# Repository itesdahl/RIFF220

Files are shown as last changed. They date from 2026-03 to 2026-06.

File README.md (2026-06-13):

# The RIFF220 DIY 3D printer
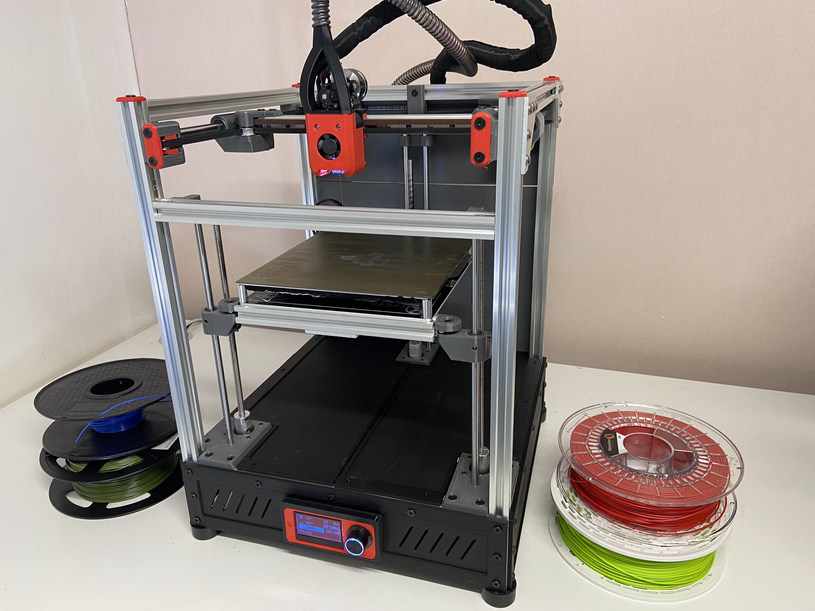
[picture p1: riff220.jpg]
Build


>[!NOTE]
>I recommend using second hand/recycled parts from old printers. It makes absolutely no sense to source all the parts new.

>[!TIP]
>Use the Voron Trident assembly guide to build the bed front arms and the A/B motor mounts. Please note that the orientation of some bolts are different from the original. You also have to replace one of the bolts with a 5mm shaft to allow the motor mout to sit flush to the top extrusion. https://github.com/VoronDesign/Voron-Trident/blob/main/Manual/Assembly_Manual_Trident.pdf Refer to the BFI idlers to print the original STLs for carrier and front. https://github.com/clee/VoronBFI
>

## Some key information the design and build:

- Max printable area 215x230x220, (X restricted by toolhead width)
- 2020 extrusions 
- 1x SKR Pico and 1x SKR 1.4 controller boards (not critical, use whatever you have that have enough drivers and can run Klipper)
- Radxa Rock 3C SBC (or a Pi. SBC with 3-4 USB ports recommended)
- MGN 12H rails/carriage X
- 10mm rods and bearings on Y 
- 8mm rods and bearings on Z 
- Corexy
- Klipper firmware 
- Triple z steppermotors (z-tilt functionality)
- Sensorless homing on X and Y 
- Dragonburner with Sherpa micro
- Low budget CPAP solution with 2 x 5015 fans (remix for ws7040 to get even more cooling)
- 1 x 240W 24V power supply

### Cutting extrusions

- 4x2020 500mm for Z 
- 8x2020 350mm for X and Y
- 1x2020 300mm for x-axis (supporting the MGN12 rail) 

### Extrusions for the bed assy in my build with a 220x220 base plate and a 214x214 24V heat bed
- 1x2020 268mm center (measure)
- 1x2020 220mm front 

>[!TIP]
>Check the frame for squareness and adjust/correct  as needed.
>Mount the 3 z-motor mounts with M5 10mm bolts. The motor mounts makes the frame more rigid. Check the frame again for squareness.

# Credits/sources for remixes
https://github.com/VoronDesign/Voron-Trident
https://github.com/clee/VoronBFI
https://github.com/chirpy2605/voron/tree/main/V0/Dragon_Burner

# Video part 1
https://youtu.be/kZbBAxifQg0

# Video part 2
https://youtu.be/Zv7GhpkNOPk

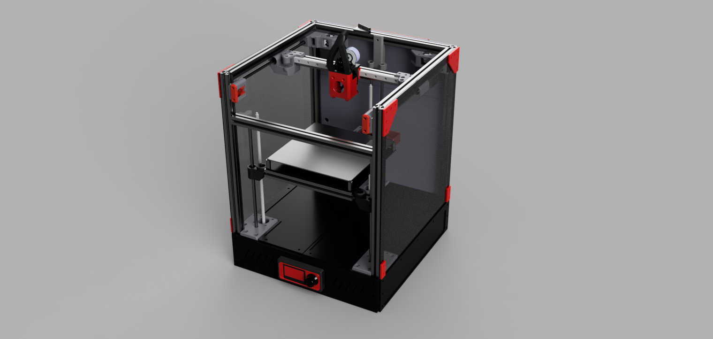
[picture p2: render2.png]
CAD model

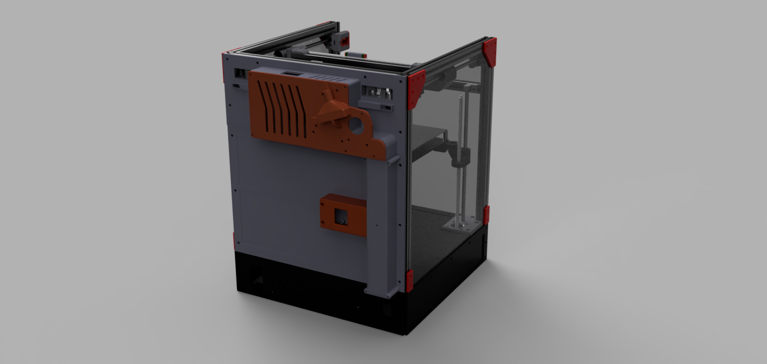
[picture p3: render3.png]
CAD model2


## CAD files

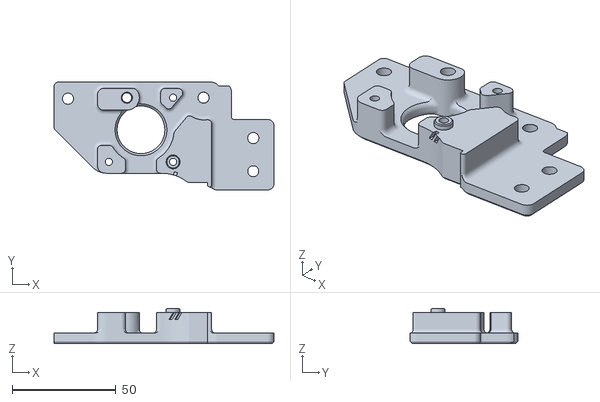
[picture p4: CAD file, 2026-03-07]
gantry/1x_rightmotor_lower.stl
106.2 x 52.0 x 17.0

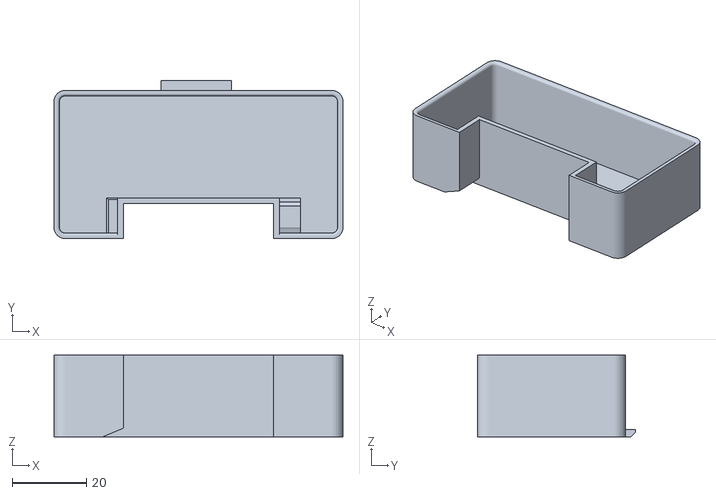
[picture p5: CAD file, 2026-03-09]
optional/1x_scrubber_bin.stl
78.0 x 42.7 x 22.0

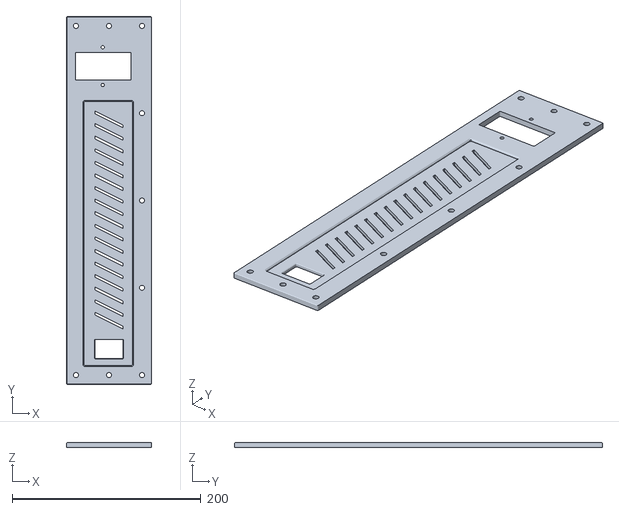
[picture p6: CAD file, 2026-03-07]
skirt/1x_rear_panel.stl
90.0 x 390.0 x 5.00

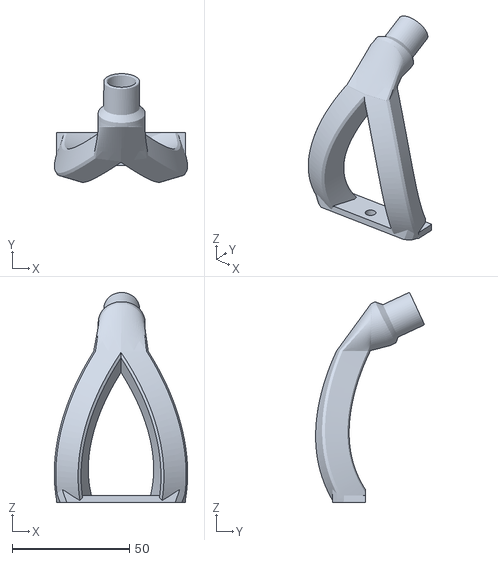
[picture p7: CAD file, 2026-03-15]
toolhead/cpap_adapter_v2.stl
56.9 x 46.4 x 89.5

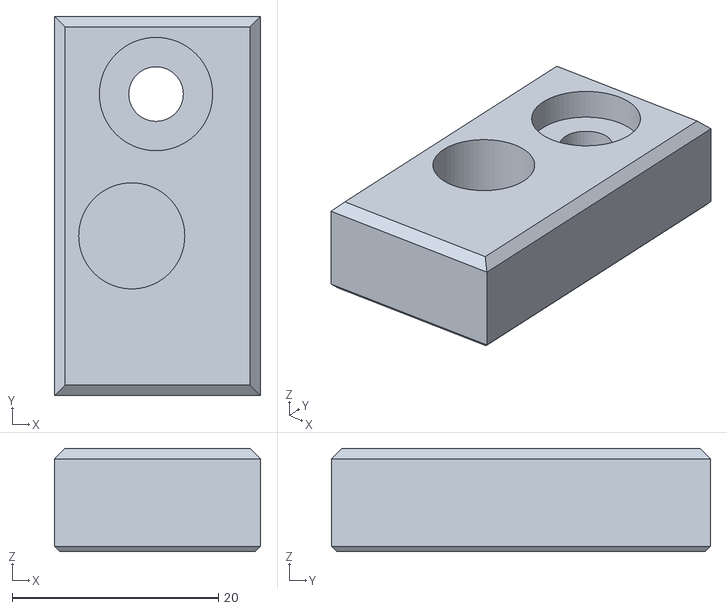
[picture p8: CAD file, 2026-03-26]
zaxis/1x_zrod_right.stl
20.0 x 36.8 x 10.0

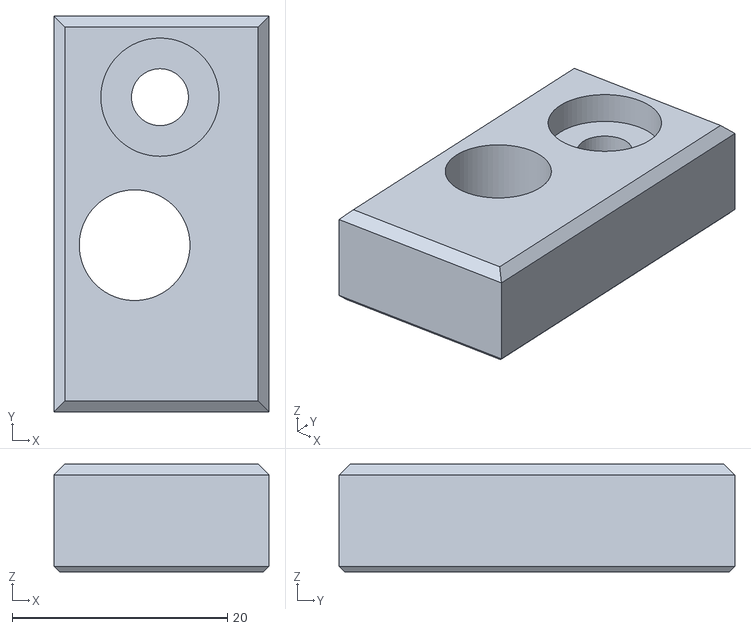
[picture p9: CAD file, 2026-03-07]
gantry/1x_yrod_right.stl
20.0 x 36.8 x 10.0

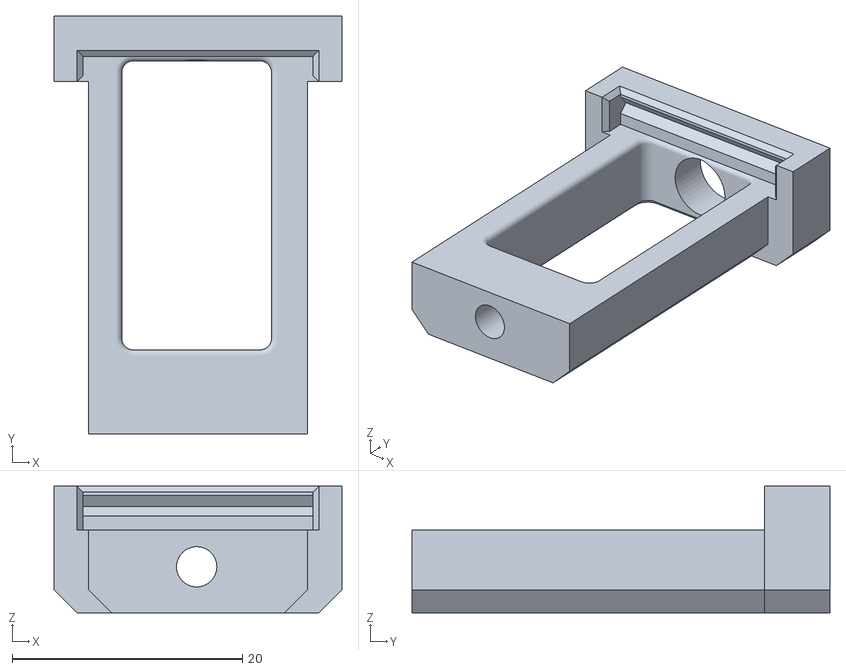
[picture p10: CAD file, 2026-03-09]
optional/1x_scrubber_holder.stl
25.0 x 36.3 x 11.0

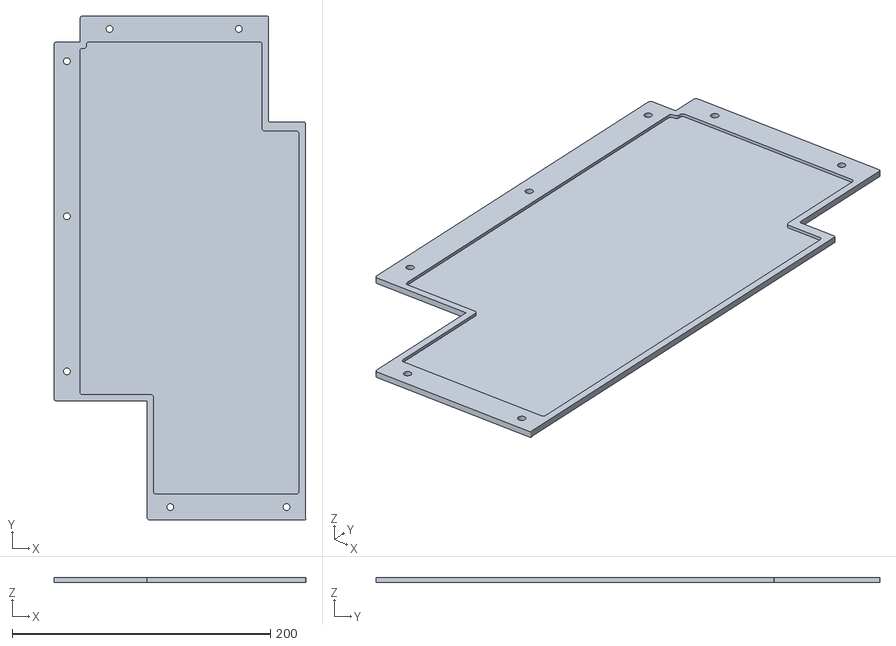
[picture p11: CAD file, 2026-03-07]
skirt/1x_left_top.stl
195.0 x 390.0 x 4.00

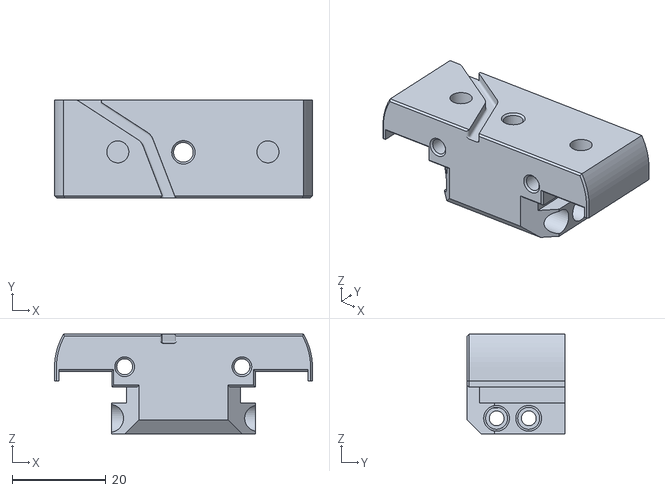
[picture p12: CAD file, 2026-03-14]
toolhead/dragon_bambu.stl
55.0 x 20.8 x 21.3

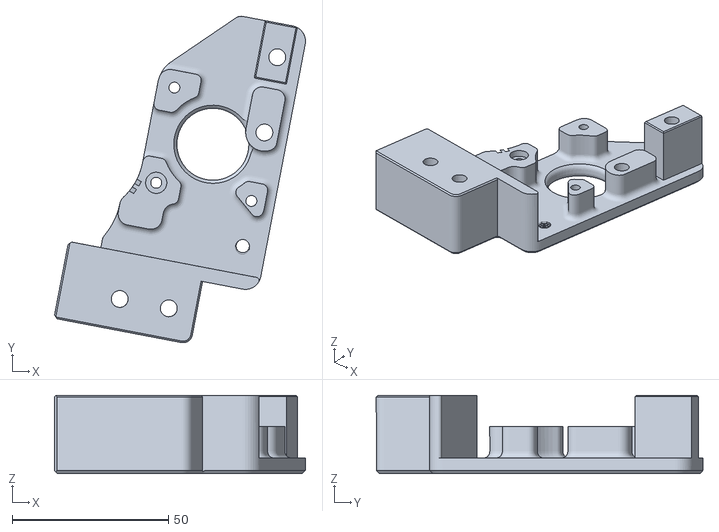
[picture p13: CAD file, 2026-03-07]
gantry/1x_leftmotor_upper.stl
80.3 x 104.4 x 25.0

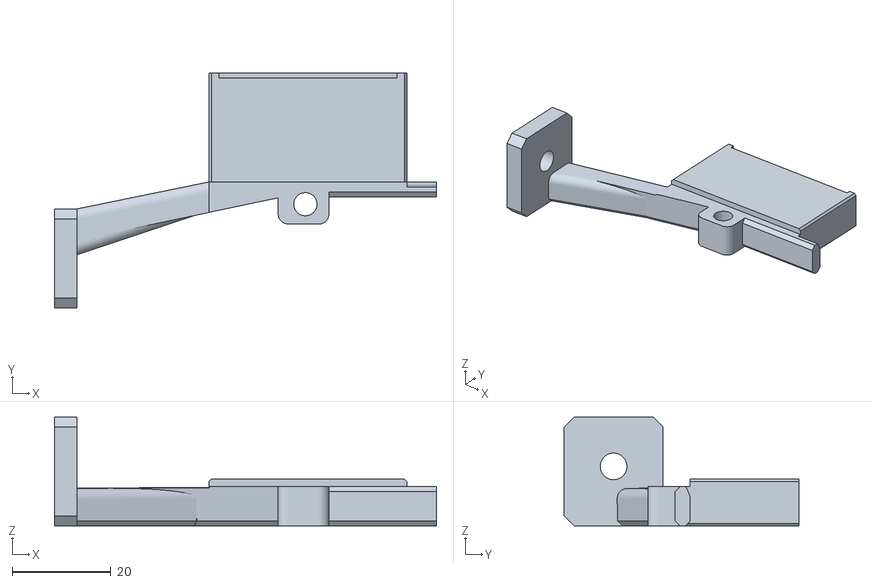
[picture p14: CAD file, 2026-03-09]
optional/1x_scrubber_arm.stl
77.2 x 47.5 x 22.0

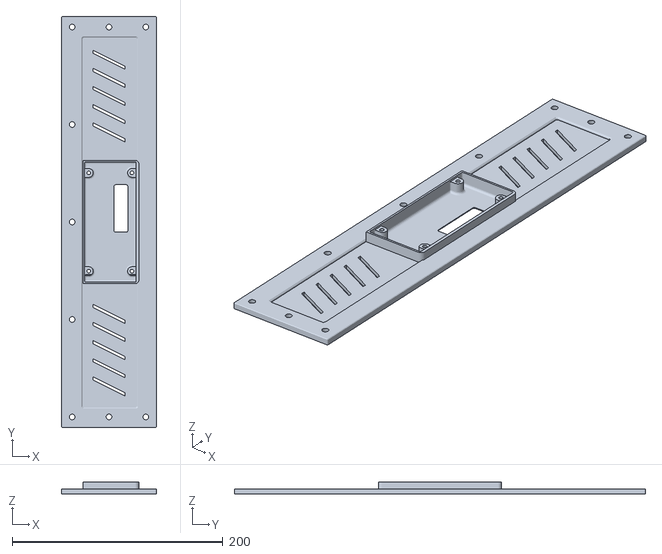
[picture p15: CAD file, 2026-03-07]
skirt/1x_front_panel.stl
90.0 x 390.0 x 11.6

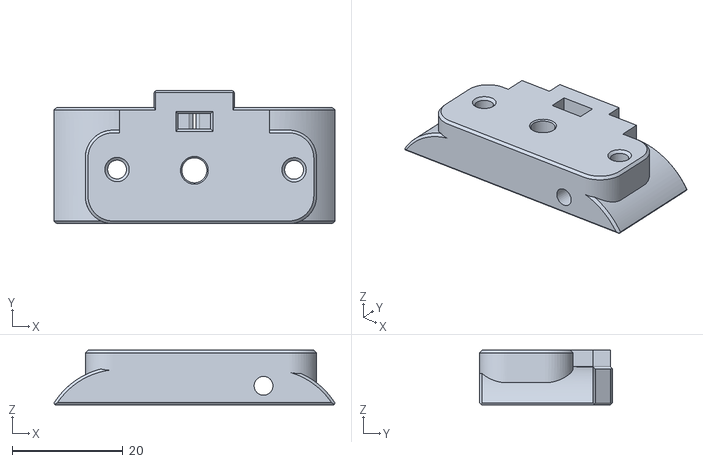
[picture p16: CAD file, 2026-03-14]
toolhead/dragon_sherpa_micro_mount.stl
50.7 x 24.1 x 9.90

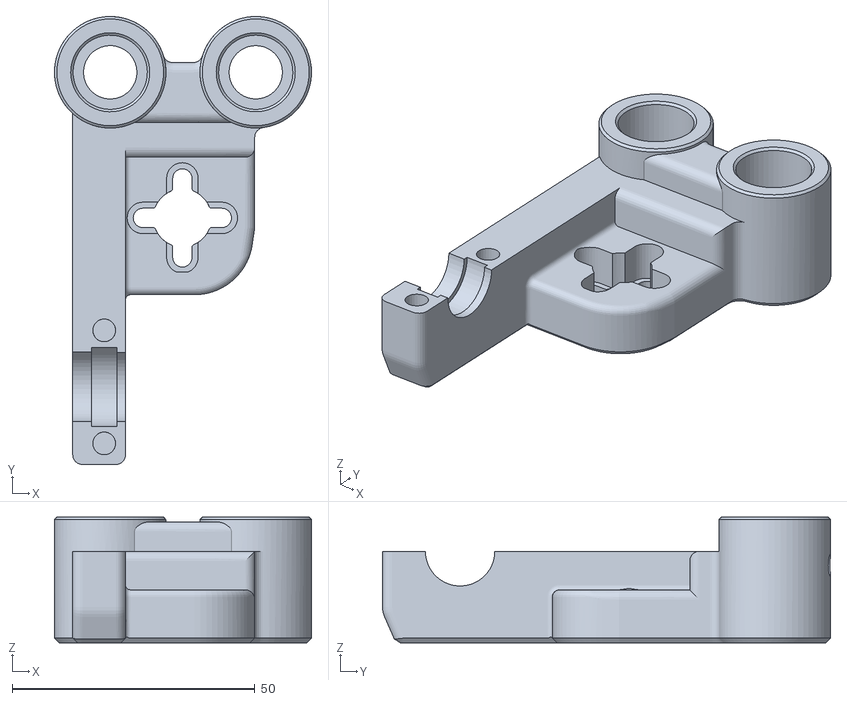
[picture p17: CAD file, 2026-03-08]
zaxis/1x_zlift_rear.stl
53.0 x 92.4 x 26.0

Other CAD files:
zaxis/1x_zrod_left.stl
gantry/2x_BFI_housing.stl
optional/1X_enclosure.stl
skirt/2x_side_panel.stl
gantry/1x_leftmotor_lower.stl
gantry/1x_rightmotor_upper.stl
gantry/1x_xy_lower_left.stl
gantry/1x_xy_lower_right.stl
gantry/1x_xy_upper_left.stl
gantry/1x_xy_upper_right.stl
gantry/1x_yrod_left.stl
optional/1x_channel_cover.stl
optional/1x_cover_cpap.stl
optional/1x_mosfetcover.stl
optional/1x_ptfe_guide.stl
optional/1x_rear_panel.stl
skirt/1x_right_top.stl
toolhead/BETA_cpap_adapter_angled.stl
toolhead/dragon_cpap_cowling.stl
zaxis/1x_GEC5_left.stl
zaxis/1x_GEC5_rear.stl
zaxis/1x_GEC5_right.stl
zaxis/1x_motormount_left.stl
zaxis/1x_motormount_rear.stl
zaxis/1x_motormount_right.stl
zaxis/1x_zlift_left.stl
zaxis/1x_zlift_right.stl
zaxis/1x_zlift_spacer.stl
zaxis/1x_zliftrear_cover.stl
zaxis/1x_zrods_rear.stl

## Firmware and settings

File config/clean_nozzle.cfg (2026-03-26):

# Inspired by https://github.com/VoronDesign/VoronUsers/blob/master/orphaned_mods/printer_mods/edwardyeeks/Decontaminator_Purge_Bucket_%26_Nozzle_Scrubber/Macros/nozzle_scrub.cfg
#######################################################################################################################################

# The goal of this macro is to provide a nozzle cleaning and purging routine that is easily copied/referenced into your printer.cfg.
# Users can simply change parameters and enable/disable options in the first half. Descriptions are plentiful, making this macro
# look huge but informative and are laid out in sequence to be read first describing the line below; PLEASE READ CAREFULLY.

# This sample config assumes the following: The user has implemented the default decontaminator purge bucket & nozzle cleaner mod
# for the VORON 1/2. It can be tweaked to customised purge bucket geometries.

# Features in this macro: option of putting the bucket at the rear or front of the bed. Purge routine that can be enabled/disabled.
# By default, bucket is located at rear left of bed and purge routine is enabled. The purge and scrubbing routine is randomized
# in either left or right bucket to ensure as even as possible distribution of filament gunk.

# Default parameters are set for safe speeds and movements. Where necessary, tweak the parameters for the nozzle scrub procedure 
# to fit your printer.

#######################################################################################################################################

[gcode_macro clean_nozzle]
# Name of the macro is clean_nozzle.

# These parameters define your filament purging. The retract variable is used to retract right after purging to prevent unnecessary
# oozing. Some filament are particularly oozy and may continue to ooze out of the nozzle for a second or two after retracting. The
# ooze dwell variable makes allowance for this. Update as necessary. If you decided to not enable purge, you can ignore this section.
variable_purge_len:            10          ; Amount of filament, in mm, to purge.
variable_purge_spd:           200          ; Speed, in mm/min, of the purge.
variable_purge_temp_min:      150          ; Minimum nozzle temperature to permit a purge. Otherwise, purge will not occur.
variable_purge_ret:             2          ; Retract length, in mm, after purging to prevent slight oozing. Adjust as necessary.
variable_ooze_offset_z:        40          ; After purging, how far up to move Z, in mm.
variable_ooze_spd_z:          120          ; After purging, how fast to move up Z, in mm/min.

# Adjust this so that your nozzle hits the tube. The nozzle should hit the upper 1/4th to 1/2nd part of the tube.
variable_tube_top:              1       ; Z position in mm

# These parameters define your cleaning, travel speeds, safe z clearance and how many times you want to wipe. Update as necessary. Wipe 
# direction is randomized based off whether the left or right bucket is randomly selected in the purge & scrubbing routine.
variable_clearance_z:           5          ; When traveling, but not cleaning, the clearance along the z-axis between nozzle and tube.
variable_wipe_qty:              3          ; Number of complete (A complete wipe: left, right, left OR right, left, right) wipes.
variable_prep_spd_xy:        6000          ; Travel (not cleaning) speed along x and y-axis in mm/min.
variable_prep_spd_z:         1500          ; Travel (not cleaning) speed along z axis in mm/min.
variable_wipe_spd_xy:        5000          ; Nozzle wipe speed in mm/min.

# Tube position
variable_tube_x:              168 # X position of tube, Y is assumed to be 0

# This value is defaulted from tube location in CAD (rear left).
variable_wipe_travel:          43 # distance to travel when claening in mm      

# These parameters define the size of your purge bucket. Update as necessary. If you decided to not enable purge, you can ignore 
# this section. A visual reference is provided below.
# 
#                                     bucket_gap
#                                      ← ---- →
#                     __________________________________________
#                    |                 |      |                 |      
#                    |                 |      |                 |
#  bucket_start (x)  |                 |______|                 |
#                    |                 |      |                 |
#                    |                 |      |                 |
#                    |_________________|. . . |_________________|
#                     ← ------------- →        ← ------------- →
#                     bucket_left_width        bucket_right_width
#  _______________________________________________________________________________________
#                                    PRINTER FRONT
# 

## For V2.4 300mm build, uncomment below
variable_bucket_left_width:    18


# These values are defaulted from bucket geometry in CAD (rear left location). Change only if you're using a custom bucket.
variable_bucket_right_width:   16            
variable_bucket_gap:           43

# For V1.8, you may need to measure where your bucket start is and input into bucket_start. Otherwise, a value of 0 is for a default
# installation of purge bucket at rear left.
variable_bucket_start: 137

###############################################################################################################################################
###############################################################################################################################################

### From here on, unless you know what you're doing, it's recommended not to change anything

###############################################################################################################################################
###############################################################################################################################################

# Placeholder. The variable will later be set to contain, at random, a number representing the left or right bucket.
variable_bucket_pos:            1
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

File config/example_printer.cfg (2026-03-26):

[include mainsail.cfg]


[mcu]
serial: /dev/serial/by-id/
[mcu xy]
serial: /dev/serial/by-id/

[virtual_sdcard]
on_error_gcode: CANCEL_PRINT


# This file contains common pin mappings for SKR V1.4 and SKR Pico
# board. To use this config, the firmware should be compiled for the
# LPC1768 and RP2040.

# For the DIY-printer RIFF220

[exclude_object]
[force_move]
enable_force_move: True

[include homing.cfg]
[include stealthburner_leds.cfg]
[include clean_nozzle.cfg]


[stepper_x]
step_pin: xy:gpio11
dir_pin: !xy:gpio10
enable_pin: !xy:gpio12
microsteps: 16
rotation_distance: 40
full_steps_per_rotation: 200
endstop_pin: tmc2209_stepper_x:virtual_endstop
position_endstop: 220
position_min: 0
position_max: 220
homing_speed: 20
homing_retract_dist: 0
homing_positive_dir: true

[tmc2209 stepper_x]
uart_pin: xy:gpio9
tx_pin: xy:gpio8
uart_address: 0
run_current: 1.02
diag_pin: ^xy:gpio4
driver_SGTHRS: 65

[stepper_y]
step_pin: xy:gpio6
dir_pin: !xy:gpio5
enable_pin: !xy:gpio7
microsteps: 16
rotation_distance: 40
full_steps_per_rotation: 200
endstop_pin: tmc2209_stepper_y:virtual_endstop
position_endstop: 230
position_max: 230
position_min: 0
homing_speed: 20
homing_retract_dist: 0
homing_positive_dir: true

[tmc2209 stepper_y]
uart_pin: xy:gpio9
tx_pin: xy:gpio8
uart_address: 2
run_current: 1.02
diag_pin: ^xy:gpio3
driver_SGTHRS: 65

[extruder]
step_pin: xy:gpio14
dir_pin: !xy:gpio13
enable_pin: !xy:gpio15
microsteps: 16
rotation_distance: 22.6789511   #Bondtech 5mm Drive Gears
gear_ratio: 50:10
microsteps: 16
full_steps_per_rotation: 200
nozzle_diameter: 0.400
filament_diameter: 1.750
min_temp: 10
max_temp: 280
max_power: 0.8
min_extrude_temp: 170
heater_pin: xy:gpio23
sensor_type: Generic 3950
sensor_pin: xy:gpio27
control = pid
pid_kp = 36.405
pid_ki = 13.484
pid_kd = 24.573
min_temp: 0
max_temp: 280

[tmc2209 extruder]
uart_pin: xy:gpio9
tx_pin: xy:gpio8
uart_address: 3
run_current: 0.500
stealthchop_threshold: 0

[probe]
pin: xy:gpio22
x_offset: 0
y_offset: 25
z_offset: 2.075
samples: 3
samples_result: median
sample_retract_dist: 3
samples_tolerance: 0.025
samples_tolerance_retries: 3

[stepper_z]
step_pin: P2.2
dir_pin: !P2.6
enable_pin: !P2.1
rotation_distance: 8
microsteps: 16
endstop_pin: probe:z_virtual_endstop
position_max: 220
position_min: -5
homing_speed: 8
second_homing_speed: 3
homing_retract_dist: 3

[tmc2209 stepper_z]
uart_pin: P1.10
interpolate: False
run_current: 0.8
sense_resistor: 0.110
stealthchop_threshold: 0

[stepper_z1]
step_pin: P2.13
dir_pin: !P0.11
enable_pin: !P2.12
rotation_distance: 8
microsteps: 16

[tmc2209 stepper_z1]
uart_pin: P1.4
interpolate: False
run_current: 0.8
sense_resistor: 0.110
stealthchop_threshold: 0

[stepper_z2]
step_pin: P1.15
dir_pin: P1.14
enable_pin: !P1.16
rotation_distance: 8
microsteps: 16

[tmc2209 stepper_z2]
uart_pin: P1.1
interpolate: False
run_current: 0.8
sense_resistor: 0.110
stealthchop_threshold: 0

[fan]
pin: xy:gpio17

[heater_fan heatbreak_cooling_fan]
pin: xy:gpio18

[controller_fan radxa_fan]
pin: P2.4
max_power: 1.0
kick_start_time: 0.5
fan_speed: 1.0 # 1.0 = 100%
idle_timeout: 999999 # Keeps it on for a long time



[bed_mesh]
speed: 120
horizontal_move_z: 5
mesh_min: 50, 50
mesh_max: 180, 180
probe_count: 6

[heater_bed]
heater_pin: xy:gpio21
sensor_type: EPCOS 100K B57560G104F
sensor_pin: xy:gpio26
control: pid
pid_kp = 63.296
pid_ki = 1.580
pid_kd = 633.725
min_temp: 0
max_temp: 105

[z_tilt]
##  Use Z_TILT_ADJUST to level the bed
z_positions:
	-45,35
	110,300
	260,35
points:
	30,25
	110,180
	180,25
speed:100
horizontal_move_z: 10
retries: 3
retry_tolerance: 0.0750

[printer]
kinematics: corexy
max_velocity: 300  
max_accel: 6000 # limits not tested
max_z_velocity: 5
max_z_accel: 100
square_corner_velocity: 5.0



########################################
# EXP1 / EXP2 (display) pins
########################################

[board_pins]
aliases:
    # EXP1 header
    EXP1_1=P1.30, EXP1_3=P1.18, EXP1_5=P1.20, EXP1_7=P1.22, EXP1_9=<GND>,
    EXP1_2=P0.28, EXP1_4=P1.19, EXP1_6=P1.21, EXP1_8=P1.23, EXP1_10=<5V>,
    # EXP2 header
    EXP2_1=P0.17, EXP2_3=P3.26, EXP2_5=P3.25, EXP2_7=P1.31, EXP2_9=<GND>,
    EXP2_2=P0.15, EXP2_4=P0.16, EXP2_6=P0.18, EXP2_8=<RST>, EXP2_10=<NC>
    # Pins EXP2_1, EXP2_6, EXP2_2 are also MISO, MOSI, SCK of bus "ssp0"


[display]
lcd_type: uc1701
cs_pin: EXP1_3
a0_pin: EXP1_4
rst_pin: EXP1_5
contrast: 63
encoder_pins: ^EXP2_3, ^EXP2_5
click_pin: ^!EXP1_2


[output_pin beeper]
pin: EXP1_1

[neopixel fysetc_mini12864]
pin: EXP1_6
chain_count: 3
color_order: RGB
initial_RED: 0.4
initial_GREEN: 0.4
initial_BLUE: 0.4


#macros from here

[gcode_macro _HOME_X]
gcode:
    # Always use consistent run_current on A/B steppers during sensorless homing
    {% set RUN_CURRENT_X = printer.configfile.settings['tmc2209 stepper_x'].run_current|float %}
    {% set RUN_CURRENT_Y = printer.configfile.settings['tmc2209 stepper_y'].run_current|float %}
    {% set HOME_CURRENT = 0.7 %}
    SET_TMC_CURRENT STEPPER=stepper_x CURRENT={HOME_CURRENT}
    SET_TMC_CURRENT STEPPER=stepper_y CURRENT={HOME_CURRENT}

    # Home
    G28 X
    # Move away
    G91
    G1 X-10 F1200
    
    # Wait just a second… (give StallGuard registers time to clear)
    G4 P1000
    # Set current during print
    SET_TMC_CURRENT STEPPER=stepper_x CURRENT={RUN_CURRENT_X}
    SET_TMC_CURRENT STEPPER=stepper_y CURRENT={RUN_CURRENT_Y}

[gcode_macro _HOME_Y]
gcode:
    # Set current for sensorless homing
    {% set RUN_CURRENT_X = printer.configfile.settings['tmc2209 stepper_x'].run_current|float %}
    {% set RUN_CURRENT_Y = printer.configfile.settings['tmc2209 stepper_y'].run_current|float %}
    {% set HOME_CURRENT = 0.7 %}
    SET_TMC_CURRENT STEPPER=stepper_x CURRENT={HOME_CURRENT}
    SET_TMC_CURRENT STEPPER=stepper_y CURRENT={HOME_CURRENT}

    # Home
    G28 Y
    # Move away
    G91
    G1 Y-10 F1200

    # Wait just a second… (give StallGuard registers time to clear)
    G4 P1000
    # Set current during print
    SET_TMC_CURRENT STEPPER=stepper_x CURRENT={RUN_CURRENT_X}
    SET_TMC_CURRENT STEPPER=stepper_y CURRENT={RUN_CURRENT_Y}

[gcode_macro START_PRINT]
gcode:
    {% set BED_TEMP = params.BED_TEMP|default(60)|float %}
    {% set EXTRUDER_TEMP = params.EXTRUDER_TEMP|default(210)|float %}
    # Heat bed for probing
    M190 S{BED_TEMP}
    # Use absolute coordinates
    G90
    M104 S180; set extruder temp
    # Home the printer
    G28
    Z_TILT_ADJUST
    # If you are generating a new bed mesh:
    BED_MESH_CALIBRATE ADAPTIVE=1
    # Move the nozzle near the bed
    G1 Z20 F3000
    # Set and wait for nozzle to reach printing temperature
    M109 S{EXTRUDER_TEMP}
    #clean_nozzle
    #absolute coordinates
    G90
    # Move Z axis up 
    G1 Z2.0 F3000 
    # Move to start position 
    G1 X10.1 Y20 Z0.2 F5000.0 
    SET_NOZZLE_LEDS_ON
    # Draw the first line
    G1 X10.1 Y150.0 Z0.2 F1000.0 E12
    # Reset extruder 
    G92 E0


[gcode_macro END_PRINT]
gcode:
    # Turn off bed, extruder, and fan
    M140 S0
    M104 S0
    M106 S0
    # Move nozzle away from print while retracting
    G91
    G1 X-2 Y-2 E-3 F300
    # Raise nozzle by 10mm
    G1 Z50 F3000
    G90
    SET_NOZZLE_LEDS_OFF
    # Disable steppers
    M84
[gcode_macro LOAD_FILAMENT]
gcode:
     M109 S230; set extruder temp
    {% set speed = params.SPEED|default(300) %}
    {% set max_velocity = printer.configfile.settings['extruder'].max_extrude_only_velocity %}
    SAVE_GCODE_STATE NAME=load_state
    M300 # beep
    G91
    G92 E0
    G1 E350 F{max_velocity} # fast-load
    G1 E25 F{speed} # purge
    M300
    M300
    RESTORE_GCODE_STATE NAME=load_state

[gcode_macro UNLOAD_FILAMENT]
gcode:
    M109 S230; set extruder temp
    {% set speed = params.SPEED|default(300) %}
    {% set max_velocity = printer.configfile.settings['extruder'].max_extrude_only_velocity %}
    SAVE_GCODE_STATE NAME=unload_state
    G91
    M300 # beep
    G92 E0
    G1 E25 F{speed} # purge
    G1 E-420 F{max_velocity} # fast-unload
    M300
    M300
    RESTORE_GCODE_STATE NAME=unload_state

#*# <---------------------- SAVE_CONFIG ---------------------->
#*# DO NOT EDIT THIS BLOCK OR BELOW. The contents are auto-generated.

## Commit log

2026-03-05 Added rear 62mm 2020
2026-03-05 Update RIFF220.zip
    Fixed rod spacing rear bracket
2026-03-07 First release of STLS
    [1x_GEC5_left.stl, 1x_GEC5_rear.stl, 1x_GEC5_right.stl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]
2026-03-07 Added optional parts/info
    [1X_enclosure.stl, 1x_channel_cover.stl, 1x_cover_cpap.stl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]
2026-03-08 Redesigned rear bed arm
    [1x_zlift_rear.stl]
2026-03-08 New rear mount
    [1x_zlift_rear.stl, 1x_zlift_spacer.stl, 1x_zliftrear_cover.stl]
2026-03-08 rev mount
    [1x_zlift_rear.stl, 1x_zlift_spacer.stl]
2026-03-09 Nozzle scrubber
    [1x_scrubber_arm.stl, 1x_scrubber_bin.stl, 1x_scrubber_holder.stl]
2026-03-12 Beta!
    Probably some issues with these
    [cpap_adapter.stl, dragon_cpap_cowling.stl]
2026-03-13 New duct
    [cpap_adapter.stl, cpap_adapter_angled.stl, dragon_cpap_cowling.stl]
2026-03-13 Renamed file
    [cpap_adapter_vertical.stl]
2026-03-13 Added beta
    [BETA_cpap_adapter_angled.stl]
2026-03-14 mounts added
    [dragon_bambu.stl, dragon_sherpa_micro_mount.stl]
2026-03-15 New adapter
    [cpap_adapter_angled.stl, cpap_adapter_v2.stl, cpap_adapter_vertical.stl]
2026-03-19 Optional cpap 2 piece print
    [1xcpap_baseplate2piece.stl, 1xcpap_funnel2piece.stl]
2026-03-19 deleted files
    [1xcpap_baseplate2piece.stl, 1xcpap_funnel2piece.stl]
2026-03-21 adaptive mesh
    [example_printer.cfg]
2026-03-26 Adedd nozzle clean code
    [clean_nozzle.cfg, example_printer.cfg]
2026-03-26 new zrodmounts
    [1x_zrod_left.stl, 1x_zrod_right.stl]
